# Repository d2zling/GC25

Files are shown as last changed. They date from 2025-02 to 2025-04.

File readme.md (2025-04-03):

<div STYLE="page-break-after: always;"><div>

# 智能物流电控技术总结

* [ ] 作者：祝晓立（D2zling）

本次物流从前期验证到最终实现所有功能花了很多时间，吸取了之前的经验，也有新技术的应用，本文章把我所完成的智能物流的电控方向所用技术总结起来，方便以后随时阅读和查看。

运行视频：[物流小车_哔哩哔哩_bilibili](https://www.bilibili.com/video/BV1aeZmYMEMx/?spm_id_from=333.1007.0.0)

---

### 着重关注问题

* **堆叠式PCB**设计
* 整机**线路走线规划**
* **易于调试**的代码架构
* **底盘**运动控制技术
* **机械臂**运动控制算法

围绕以上问题，结合结构和视觉的需求，电控开始进行从硬件电路到软件驱动、算法层面的全面设计。

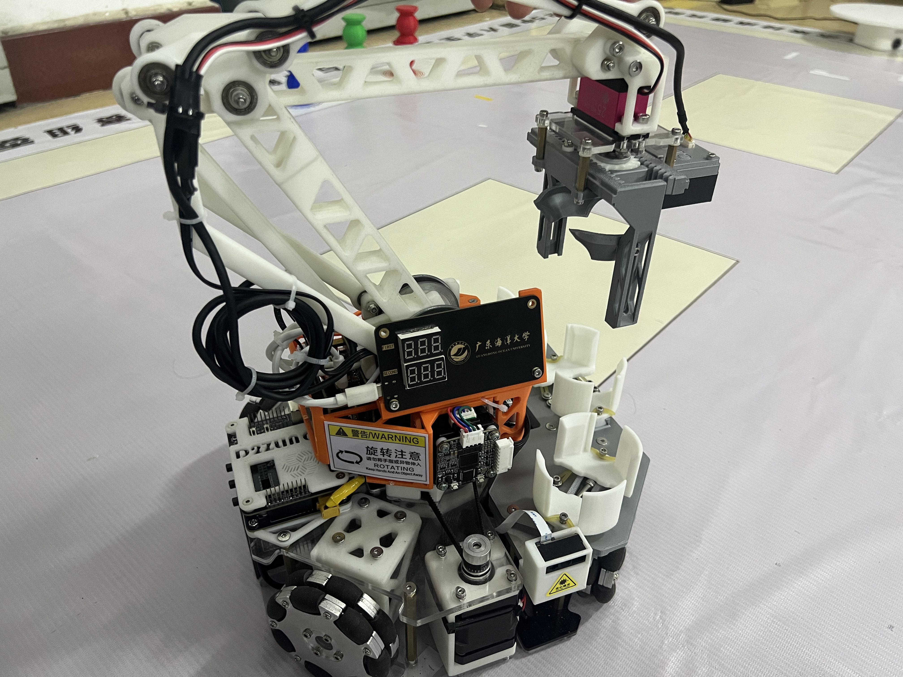
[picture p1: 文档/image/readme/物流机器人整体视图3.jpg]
整体视图


---

### 硬件设计

#### 概览

本次PCB最重要的设计思路就是堆叠式PCB设计，堆叠式PCB可以实现更快的**电路维修**，替换，实现电路的**模块化**，充分利用**垂直空间**。例如功率板和主控板的堆叠设计，充分利用了物流车的垂直空间，调试时主控板损坏，又或者主控板需要替换升级，我们只需要替换掉主控板就可以了，不需要维护功率板。截止到校赛，一共设计了四块PCB，分别是**功率板**、**主控板**、**云台顶部、底部分线板、**显示板、灯光板、泰山派拓展版等。功率板连接电池，负责整车电源控制，主控板使用**STM32F4**主控，引出多种通讯接口，满足各种外设控制需求。分线板通过40pin的FC排线连接主控板，然后引出各种接口，接电机、树莓派（泰山派）等设备。显示板使用74hc595串行芯片实现控制数码管显示任务码。具体文件可以参考[PCB\25工创PCB.eprj](./PCB/25工创PCB.eprj)文件，PCB文件使用嘉立创绘制。

<div STYLE="page-break-after: always;"><div>

* 下图展示各块PCB的连接方式

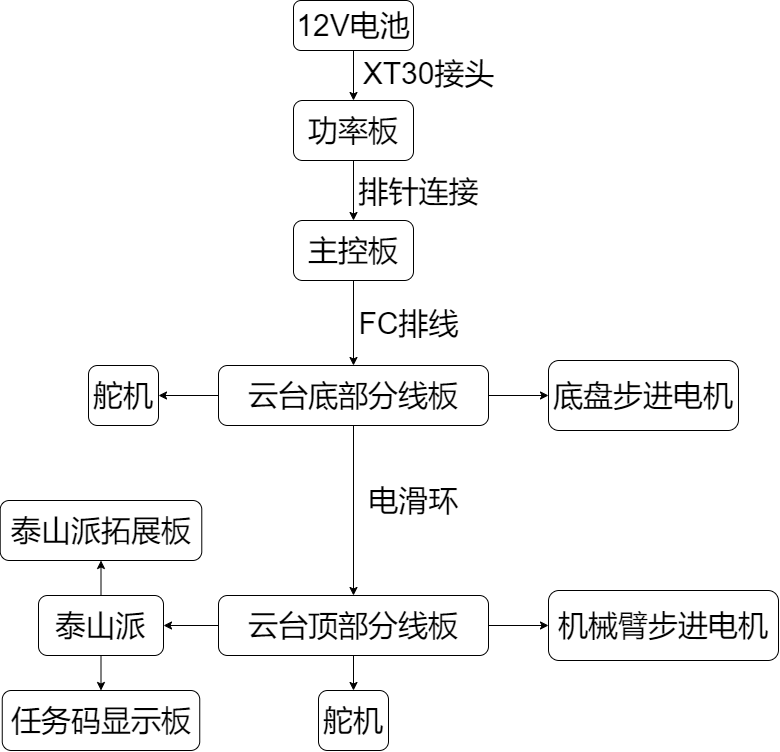
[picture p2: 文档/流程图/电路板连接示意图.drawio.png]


#### 功率板

功率板具有升压和降压功能为整个物流车提供电源，搭载两路升压电源和两路降压电源，升压使用传统**boost**拓扑电路从电源电压**12v升压到24v**，供电机或者其他需要高功率用电器使用，使用**XL6019**，有最大5A的开关电流，因为电机功率比较大，这里选择两路同样的升压芯片，每路XL6019驱动四个步进电机，总共驱动八个。降压使用**buck**拓扑电路，分为两种降压电压，分别是降压到6v和5v，降压到**6v**给舵机使用，降压到**5v**给芯片、树莓派（泰山派）等使用，使用的是**TPS5430ADDR**，可以输出3A的连续电流，还是**宽输入**的可以输入5.5V到36V，对于驱动一些芯片或者舵机来说绰绰有余。更加具体的芯片信息可以从他的**数据手册**上找到，包括输出电压调整，典型应用等，这里不再赘述。

在设计功率板时，除了**电路完整性**之外，还要注意每个部分使用起来是否**便利**，比如功率板在设计时，我将三路（24v、6v、5v）电源输出都做了**单独开关**，调试物流车时可以单独开关三路电源，更加方便调车。另外要从升降压芯片**输入端**做开关控制，防止功率板关断不完全，如果从芯片输出端做开关控制，虽然电源开关是关断了，但是实际芯片还在从输入端供电，持续损耗电源的电，也就是没有完全断电。功率板输入接口选择**XT30**，这个接头是航模接头，很稳固，大小合适而且也好看。电源输入端还连着一个DC接头，有了这个DC接头，不但可以多一个电源输入接头，能兼容更多电池接口，平时还可以实现不断开电池的XT30接头，直接用这个DC头充电，更加的便利。大家设计PCB时可以参考功率板的设计，都是经过测试的方案，基本不会出现问题。另外在设计电路接口的时候，还可以多多上**淘宝**看看各种连接器，比如一些加高排母等连接器，可以让你的PCB调车的时候使用起来更加便携。

* 功率板原理图

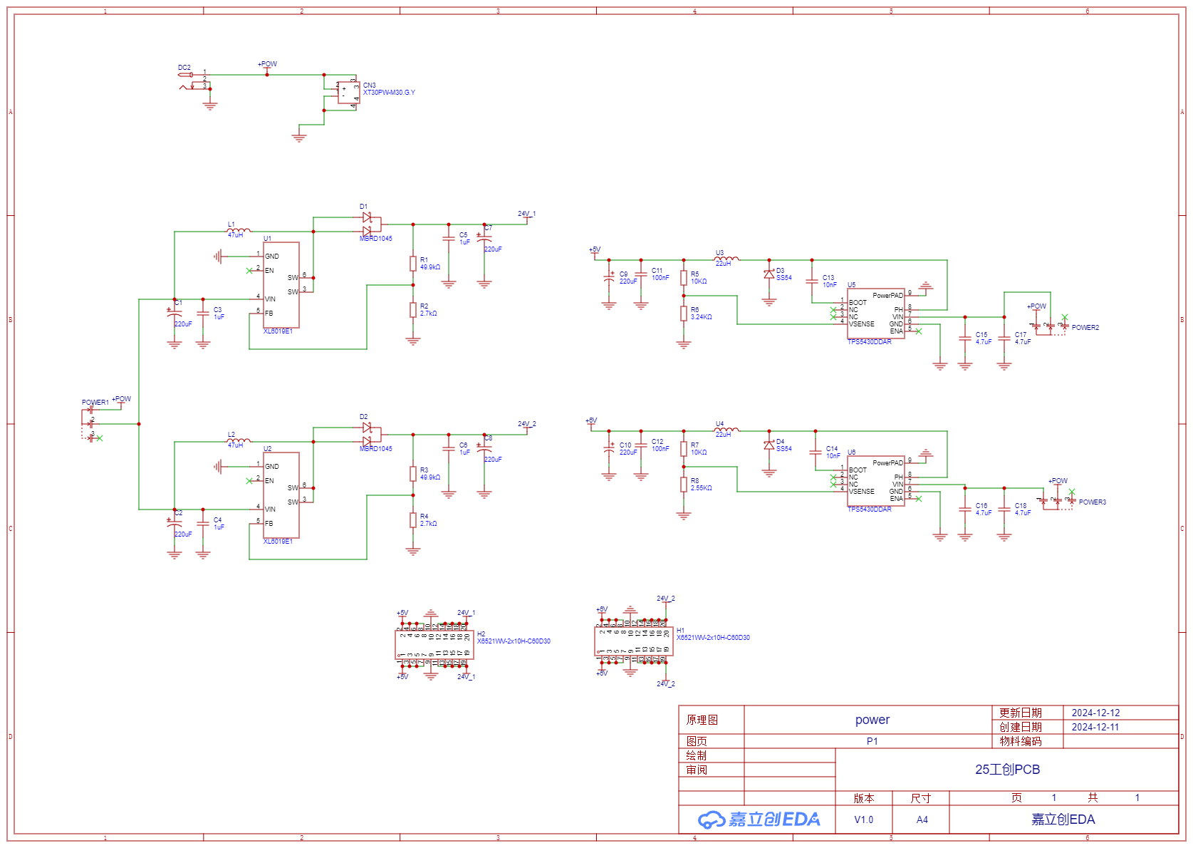
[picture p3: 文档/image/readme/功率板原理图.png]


功率板的**布局布线**要特别注意，因为是控制电源的，如果电源不稳，会出现很多莫名其妙的问题，重打一块PCB的时间成本一般在6~10天时间成本是很高的，所以我们设计PCB要争取一版做好。功率走线一定要粗，这里的功率走线使用了铺铜+开窗的方法增大过流能力，开窗之后可以在铜箔上铺一层锡，增大过流面积，下图使用黄色线勾勒的铜箔就是使用铺铜+开窗增大过流能力的例子。电源除了铜箔走线要粗，反馈线也要布局好，**反馈线很大程度上决定了电源稳不稳定**，下图标了数字1234的四条导线都是反馈线，无论是buck还是boost电路，都有**反馈（FB）引脚**要从输出电容附近取电，因为经过输出电容的电压是最稳的，最适合来做电压反馈的。设计电源的时候要分清哪些是**功率走线**，哪些是**信号走线**，功率走线尽量短和直，还有一定要够粗，信号线要走干扰少的地方，高频回路面积要小。另外，在可能发热的地方还可以多打散热孔，像是功率板的XL6019底下和TPS5430ADDR底下都有几个过孔增加散热。

* 功率板底层layout

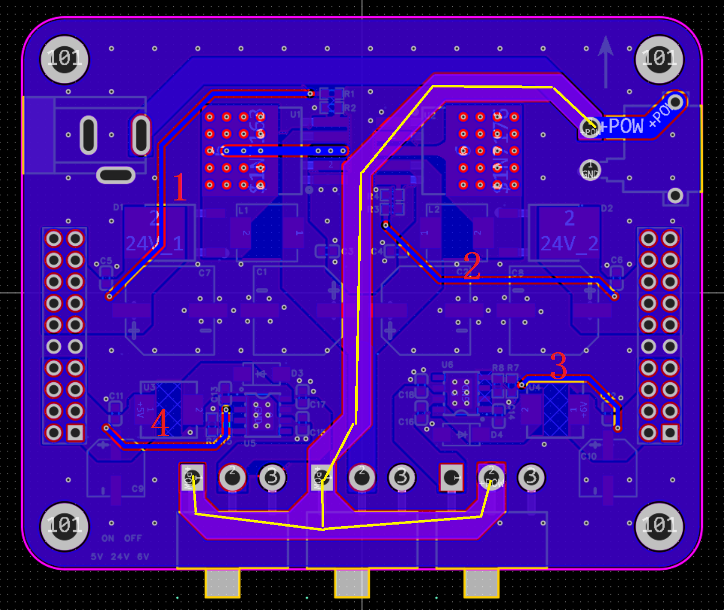
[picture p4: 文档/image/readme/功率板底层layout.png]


由于功率板涉及到**堆叠pcb**设计 ，在设计的时候我们并不确定某些元器件会不会和另外一块电路板有**干涉**，所以我们可以充分利用嘉立创的导出3D模型的功能，导出step文件，利用**solidworks**将两块电路板组合成一个装配体，可以大概的查看元器件有没有干涉，如下图所示。

* 3d模型图

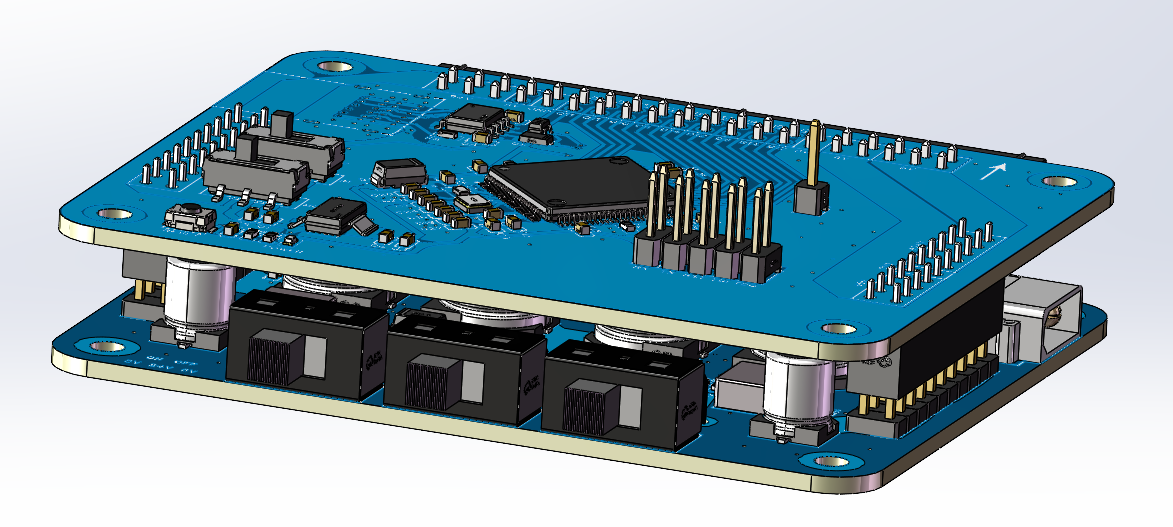
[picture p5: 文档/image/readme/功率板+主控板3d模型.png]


#### 主控板

主控板是整个物流车的核心，主控使用的是**STM32F407VET6**，选择这颗芯片的原因是第一个熟悉，第二个价格合适，外设刚好够用，性能绰绰有余，主控板集成了一个**CH340N**串口转USB芯片和一个**AMS1117**降压芯片，给芯片提供3.3V工作电压。还有两个**单独**开关，分别控制双层typec接口的电源和芯片的电源，设计上可以单独打开芯片或者typec电源，更加便于调试。还留了一个**无线DAP烧录器**的调试接口，支持远程串口，可以远程下载程序。主控板的布局布线比较简单，只要能连通基本就能工作，但是要注意，芯片的**去耦电容**要摆放在芯片的供电引脚旁边，保证电源的质量，去耦电容的**大小和数量**在芯片手册可以找到。主控板通过一个40pin的FC排线输出信号和电源，有12路24V电源，4路6V，两路5V，剩下的都是信号线，大部分时串口线，还预留了4根引脚，可以扩展功能。

* 主控板顶层layout

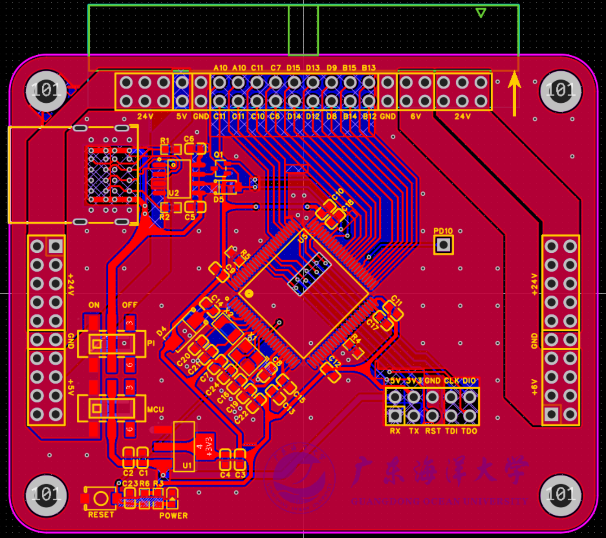
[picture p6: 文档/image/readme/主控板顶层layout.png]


主控芯片的原理图可以直接使用，STM32F407的**PD10**引脚单独引出的原因是为了**测量程序运行的时间**，在程序需要计时的地方加一行反转PD10引脚的电平然后配合示波器就可以测量出程序运行的时间，可以看整个系统的时间响应情况。主控板原理图里比较有意思的是CH340N的**防倒灌电路**由一个二极管和一个三极管组成，在CH340手册里面有描述它们的作用，这里的主要目的是为了防止视觉模块通过CH340N的**TX和RX引脚**反向供电给STM32导致STM32无法关机，之前就遇到过**关闭不完全**的情况，导致芯片看上去断电实则还在运行，调试的时候就没那么方便。板载还有一颗LDO用的是常用的AMS1117，是用于5V降压到3.3V。目前只有一个指示3.3V的LED，主控板之后还可以改进给每一路电源做一个LED显示是否开启，不然在调试的时候经常分不清哪些开关时打开的，哪些时关闭的。

<div STYLE="page-break-after: always;"><div>

* 主控板原理图

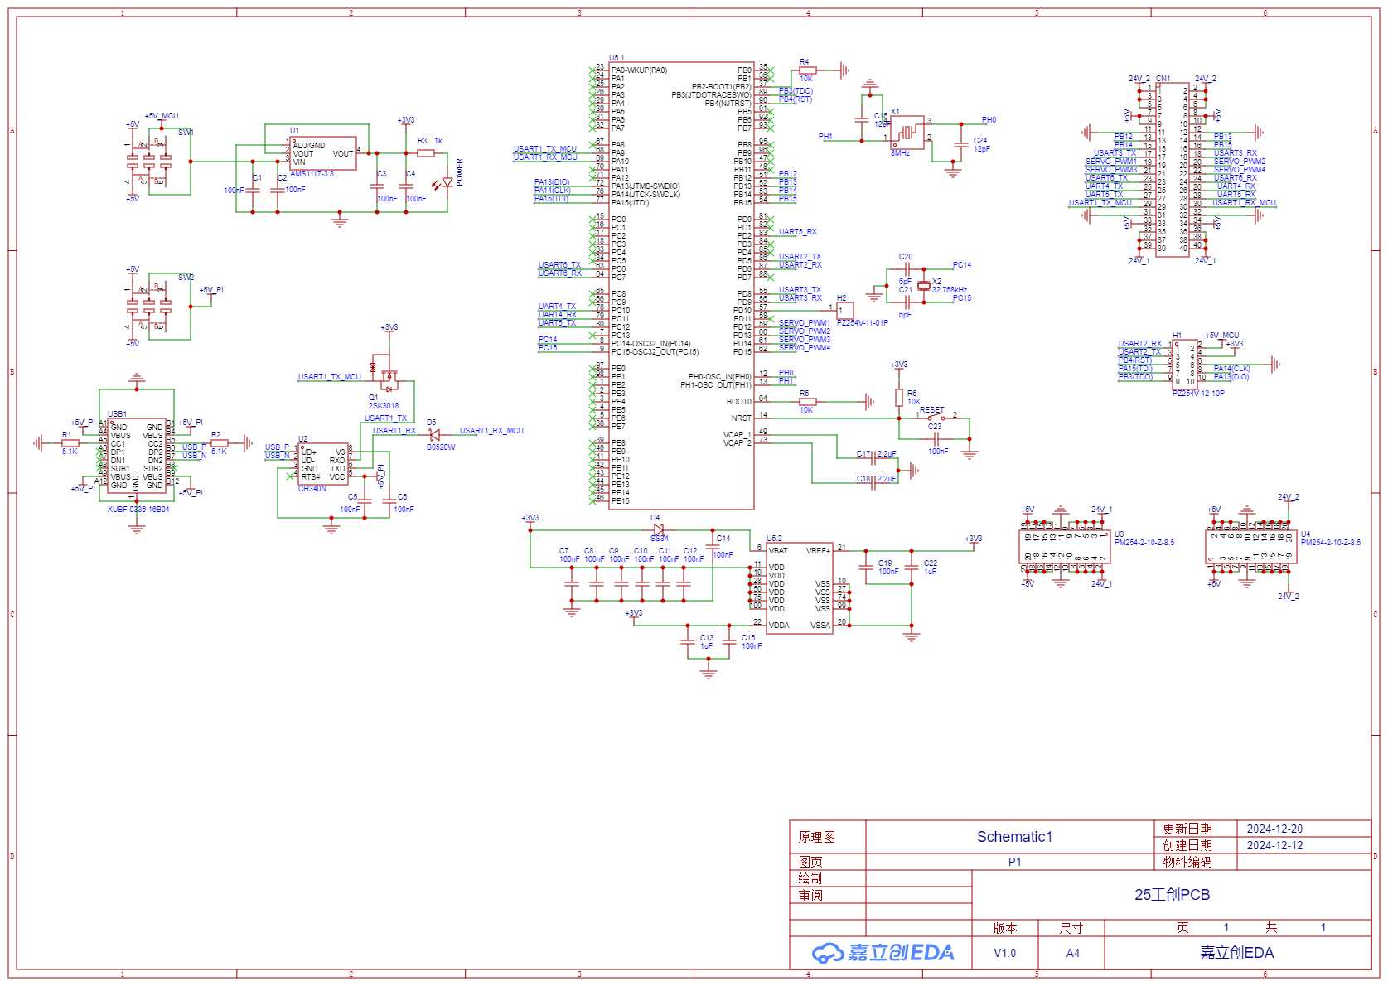
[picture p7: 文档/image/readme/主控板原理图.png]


* 功率板+主控板堆叠设计实物图

<div style="text-align: center;">堆叠设计</div>

可以注意到的是，功率板和主控板设计了很多**开关**，加起来一共有五个， 下面三个是控制24V、6V、5V的上面两个是在5V的基础上再加两个开关，控制5V上的主控芯片和外接视觉模块的供电，这样的好处是我们可以**单独调试**某些功能，而让其他功能不工作。举个例子，如调试舵机的时候，我不希望电机上电，那么我们只要接通6V和5V和主控芯片的电源就可以调试了，电机是完全断电的状态，可以加快工作效率。

#### 分线板

设计分线板的目的是为了**更简洁**的接线，还有把**陀螺仪**放在物流车的**机械中心**。分线板分为**两块**，一块是在云台下面，另外一个是云台上面，通过电滑环连接。分线板大部分是接口元件，还有一个AMS1117从5V降到3.3V供陀螺仪使用。由于分线板是放在机器内部，比较难拆出来，所以设计的时候就想着要电路要简洁可靠，基本没有什么元件，这样才可靠性高，可靠性高意味着不用经常拆出来维护，最终设计出来的效果也确实如此，上面只有两个元器件，一个是降压芯片还有一个陀螺仪，其他都是接口，连接电机、舵机等各种设备。平时容易出问题的PCB都放在机器外面比较好拆卸的地方，通过一个40pin的FC排线连接分线板，拆卸的时候只要拆出排线和几颗螺丝就能拆除主控板和功率板，这种设计更能提高维护效率。在设计分线板的原理图的时候要注意**FC排线线序**的问题，不然线序错了接上就烧了。

* 云台底部分线板原理图

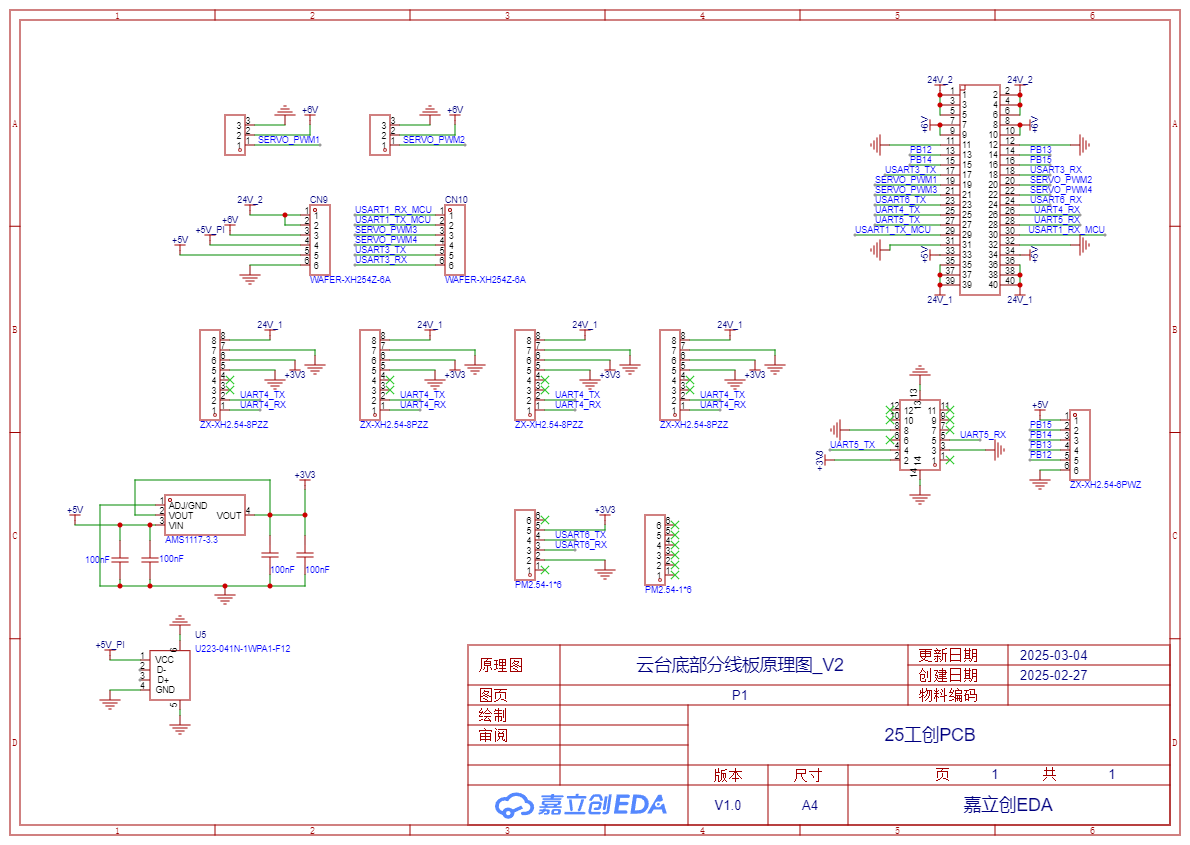
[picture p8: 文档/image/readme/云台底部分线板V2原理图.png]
分线板


PCB的外形可以让结构同学规划，然后把DXF文件导出，利用嘉立创的DXF文件导入功能就可以导入外形文件，这样就不用担心外形会冲突，分线板的外形就是结构同学规划的。关于分线板的layout基本不用注意什么东西，只要功率走线够粗就行，最主要的是设计的要便利，分线板出线位置要和电机等设备的位置一一对应。关于连接件的选取可以多逛逛淘宝，很多方案都是在淘宝看到才了解到的，比如是主控板的双层typec接口。

* 云台底部分线板顶层layout

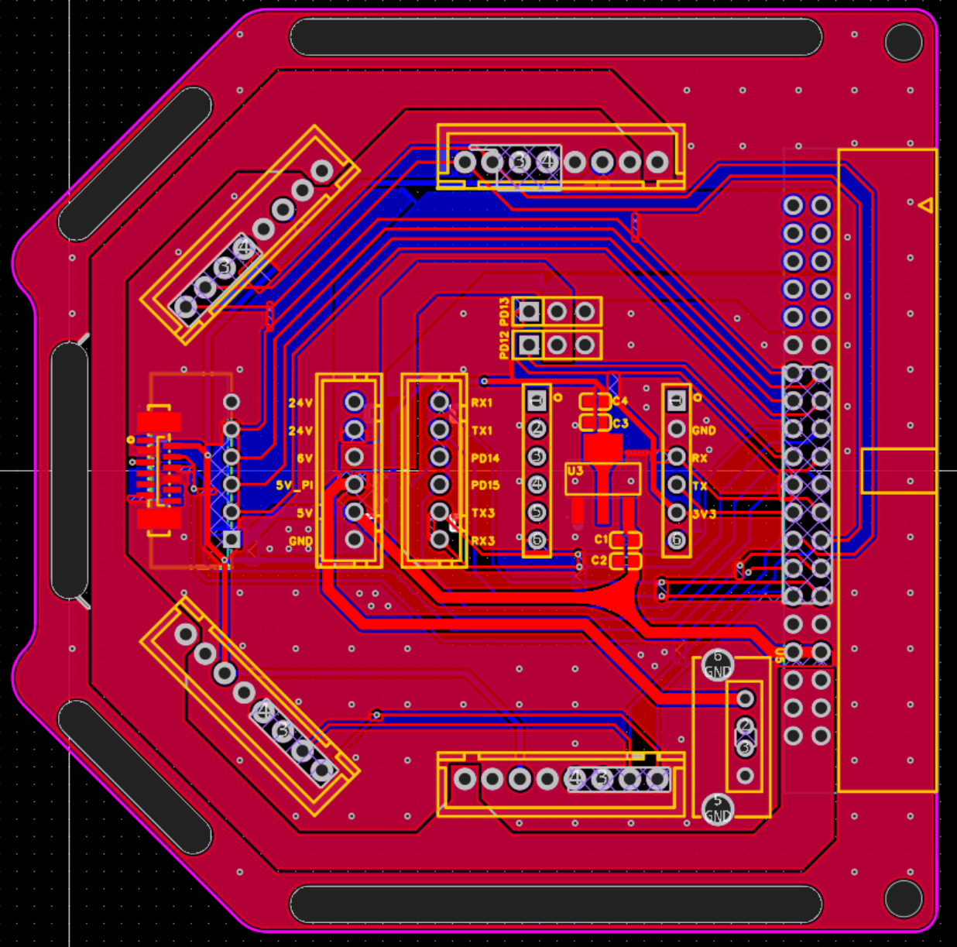
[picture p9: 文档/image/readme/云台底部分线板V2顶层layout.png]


* 云台顶部分线板原理图
  云台顶部分线板预留了泰山派供电，泰山派通讯，云台电机通讯，舵机控制。

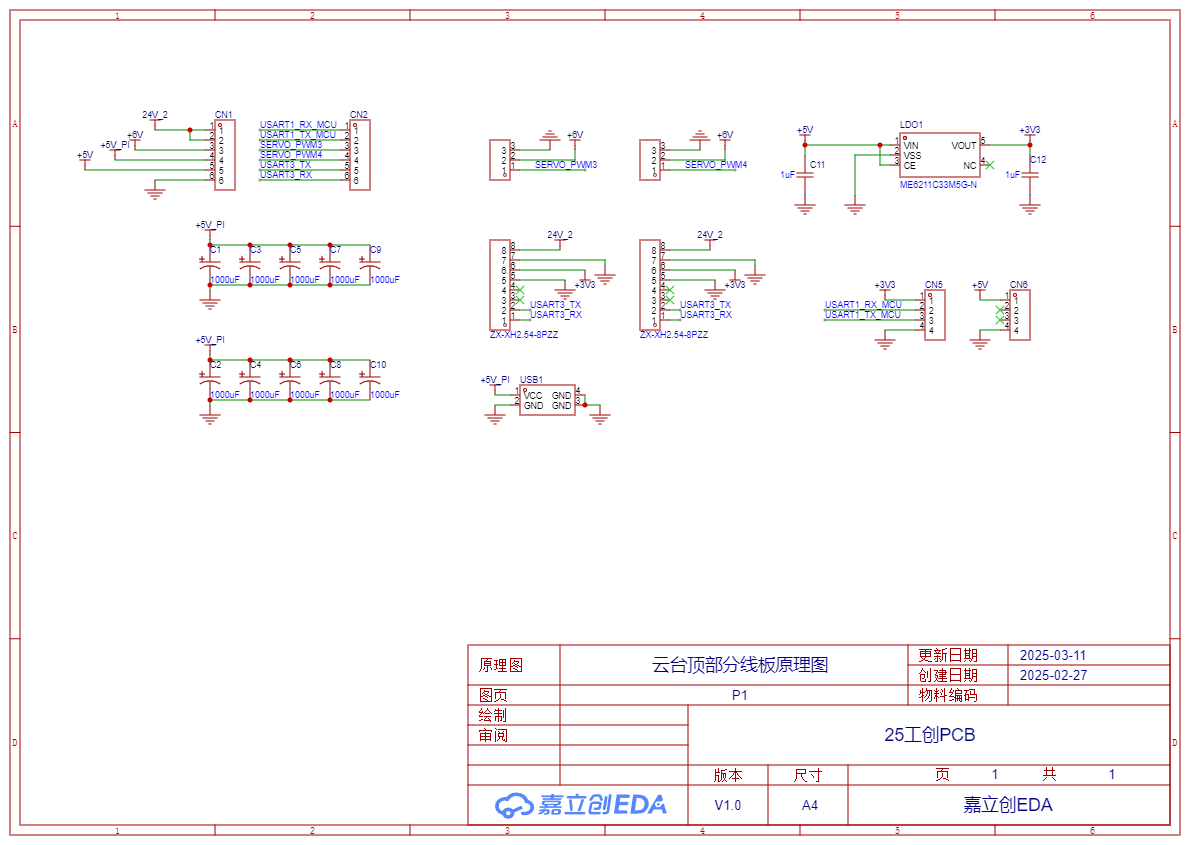
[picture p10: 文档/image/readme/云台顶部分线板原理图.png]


* 云台顶部分线板layout

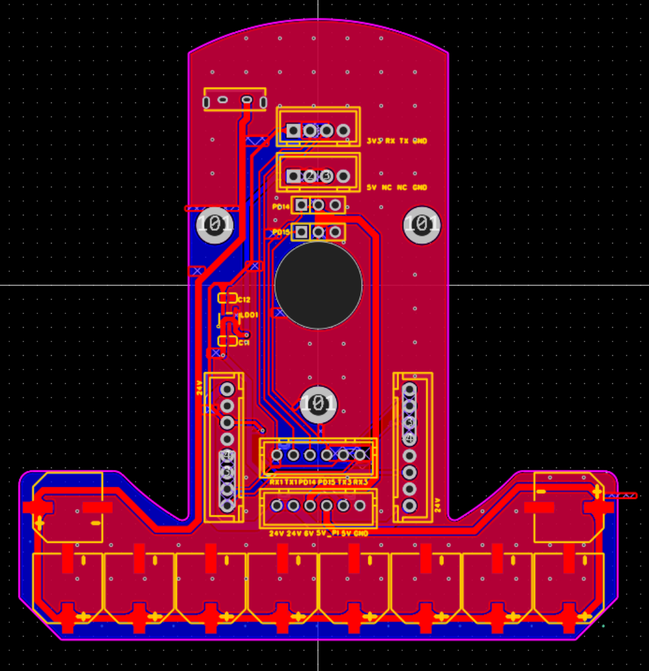
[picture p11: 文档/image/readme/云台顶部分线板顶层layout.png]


顶部分线板在给视觉模块（泰山派）那路装了很多电容，全部加起来有1F，设计的目的是放置泰山派在电机启动时造成整车低电压导致泰山派重启。

#### 显示板

* 显示板原理图

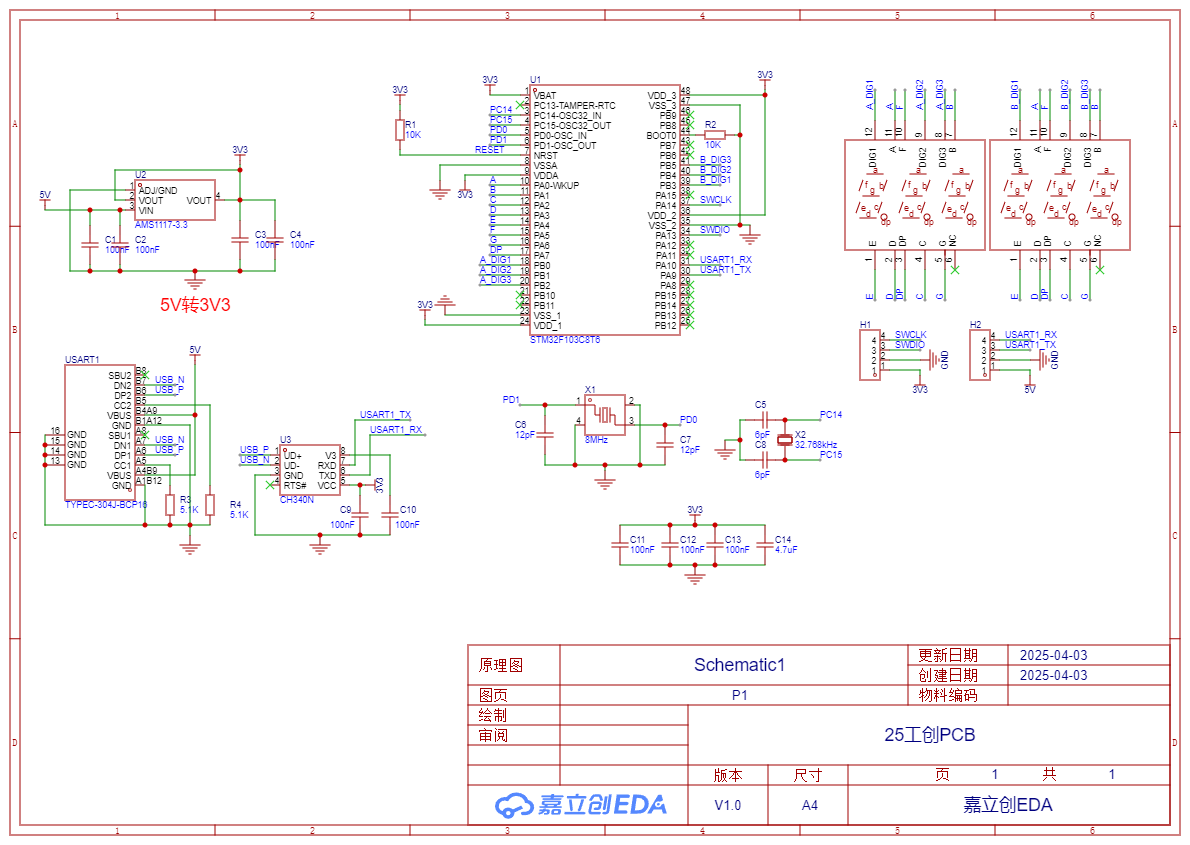
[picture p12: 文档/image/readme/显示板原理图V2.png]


* 显示板顶层layout

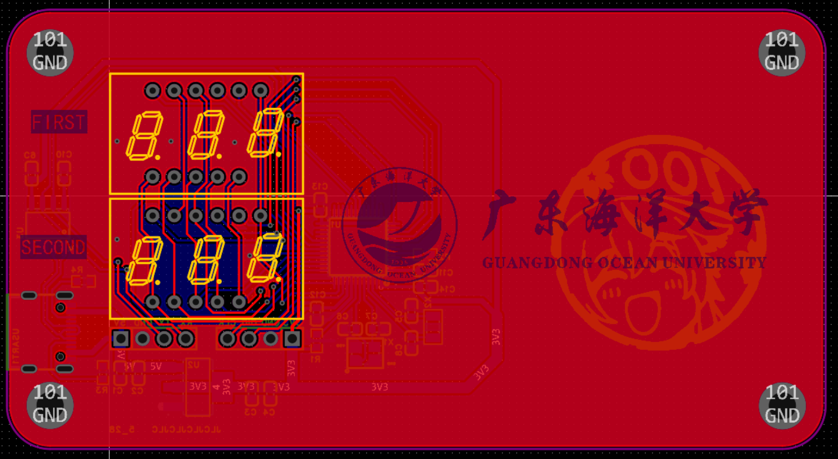
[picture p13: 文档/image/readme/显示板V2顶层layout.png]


#### 灯光板

灯光板设计目的是为了给视觉补光，做了个环形光源。使用stc15w204s单片机，仅有8根引脚，十分适合来控制rgb灯珠。灯珠用的是ws2812。

* 灯光板原理图

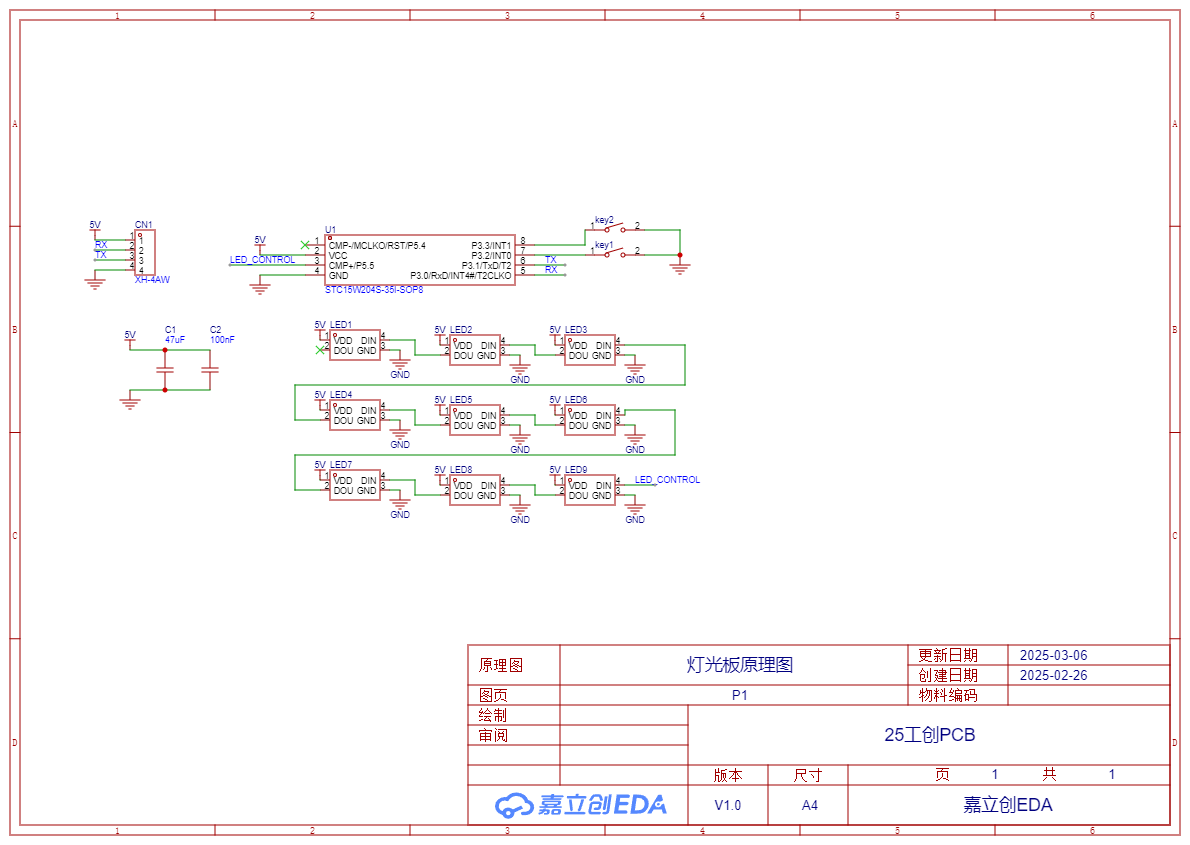
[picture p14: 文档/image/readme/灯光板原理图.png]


如下图所示环形光源

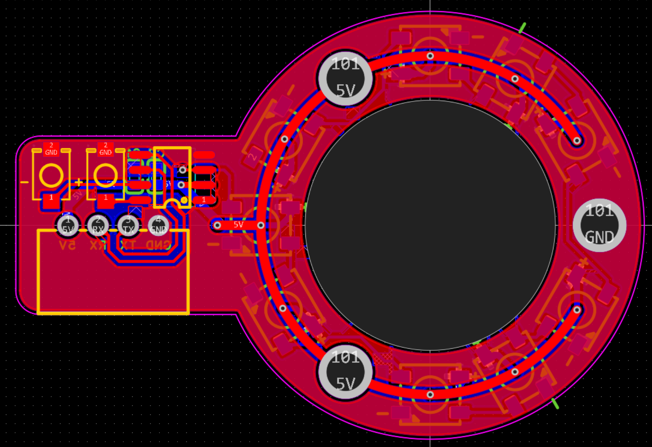
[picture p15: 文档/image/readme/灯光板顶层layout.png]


#### 泰山派再拓展版

此PCB见视觉部分文档。

#### * **注意**

1. 在功率板上并没有集成3.3V电压的降压芯片，因为3.3V电压太低，容易受干扰，最好在需要3.3V的场合单独接一个**AMS1117**或者其他替代LDO芯片，来给STM32F407和其他需要3.3V的使用。舵机单独6V原因是因为舵机的电流大，与其他用电器共一路会引起电压波动，严重的会造成树莓派等重启。
2. ~~目前电路板还存在电机上电时**电压不稳**的情况，推测是电池的电流输出能力不够或者升降压芯片的动态响应不够好的原因，会在电机上电时造成其他路有个瞬间低电压，造成其他路设备重启，可以尝试**增大输出电容**来解决这个问题。~~（已解决，解决方案在顶部分线板与泰山派连接的5v电源升压到6v，另外添加1F电容作为低谷储能电容，实测5000uf电容就可以）
3. ~~主控板的双层typec接口目前会概率出现无法识别的情况，估计是识别电阻的问题，可以通过换用更熟悉的单层typec接口来解决或者是尝试更换识别电阻。~~（已解决，解决方案直接使用stm32f4串口连接视觉设备串口，不通过USB）
4. ~~为了显示板的布线考虑，原理图74HC595连接数码管的方式是乱序的，编写驱动程序的时候要注意。~~（74HC595芯片的显示板不使用，原因：电路板功能验证未通过，改用V2任务码显示板）

---

<div STYLE="page-break-after: always;"><div>

### 运动算法设计

#### 概览

工程使用的算法大概可以分为三种，分别是底**盘控制**算法，**机械臂控制**算法，5阶**插值**算法。

#### 底盘控制算法

关于底盘的控制算法，不同的驱动方式有不同的算法，经过考虑，整车选择了全向轮作为驱动机构，四个全向轮组成**O**形，实现全向移动。算法原理很简单，只需要用到速度矢量的分解，三个速度矢量分别是方向x速度、y方向速度和角速度w，其中x和y垂直且与组成的平面平行于地面，分解为四个全向轮的速度。

具体推导可以参考以下文章：`https://blog.csdn.net/weixin_42722140/article/details/134621461`

需要注意的是文章通过一个**旋转矩阵**实现了从物流车坐标系到世界坐标系的转换。

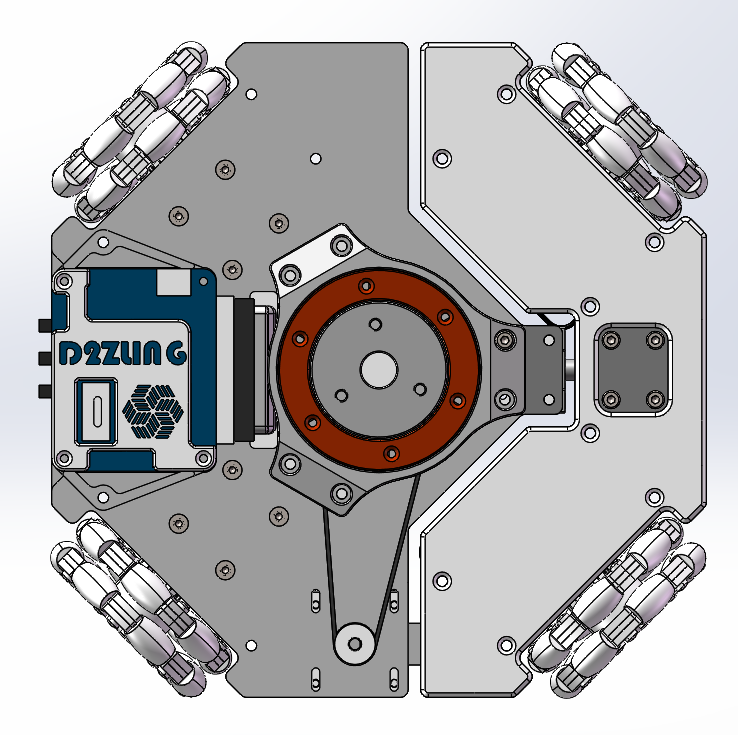
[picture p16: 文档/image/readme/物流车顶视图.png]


#### 机械臂控制算法

机械臂运动学解算分为机械臂运动学正解算和逆解算，正解算是由各个关节的角度推算机械臂末端坐标，逆解算是由机械臂末端坐标推算各个机械臂关节的角度。逆解算用于**控制**，正解算用于机械臂**示教**（校赛暂未实现）。

* 值得注意的是，机械臂算法并没有刻意的去解算计算xy的平面（机械臂底部电机）的角度，仅解算yz平面的角度（大臂角和小臂角度）。xy平面的角度将分离为一个单独调整的变量来控制，这样做的**目的**是更方便的调试动作。

机械臂运动学逆解算算法可以参考以下视频：

```
https://www.bilibili.com/video/BV1mY411476h/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
```

机械臂正解算的思路就像点在平面坐标系移动，已知机械臂的各个臂长和角度，通过三角函数可以推算出每一段的点的x和y所走的距离，叠加各段x和各段的y，最终得到末端坐标。

#### 5阶插值

关于五阶插值的原理可以参考以下文章：`https://www.zhihu.com/tardis/zm/art/269230598?source_id=1005`

简单来说，插值在本工程运动算法的作用是让一段运动变得丝滑，特别是底盘控制，若合理的设置节点的时刻、位移、速度、加速度，5阶线性插值算法能自动解算出一段路径的每个时刻的速度，让物流车运行更加的平稳，**防止车轮打滑**。

前文提到，本次物流车底盘控制算法在底层就是控制x、y、w方向上的速度，在此基础上，分别对这三个方向进行插值，即可实现对一段平滑的轨迹进行控制。下图展示的使用 `matlab`仿真设定x和y方向的每个节点位移、速度、加速度，自动解算出中间过程数值的结果。可以看出，在速度、加速度都是连续的，意味着运动的丝滑。

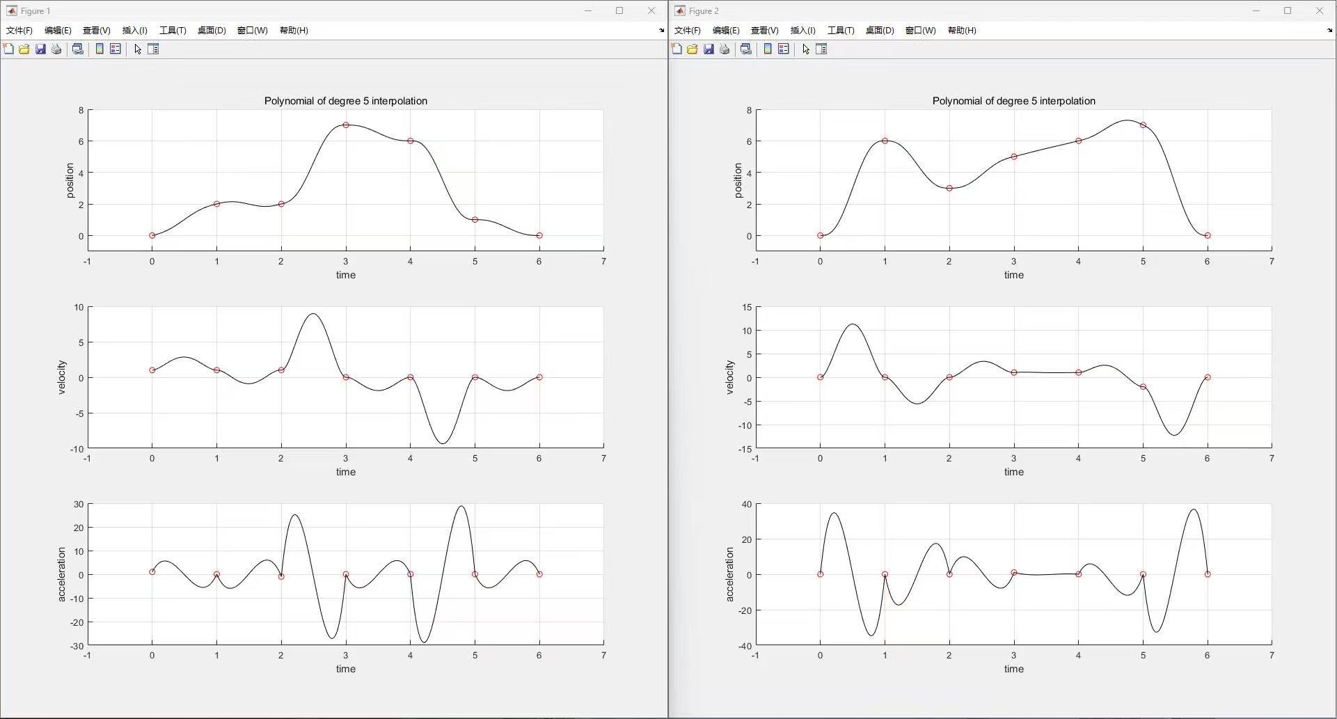
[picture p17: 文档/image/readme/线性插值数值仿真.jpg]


把x和y上的位移作为坐标系的横轴和纵轴，我们可以得出**模拟轨迹**图如下。

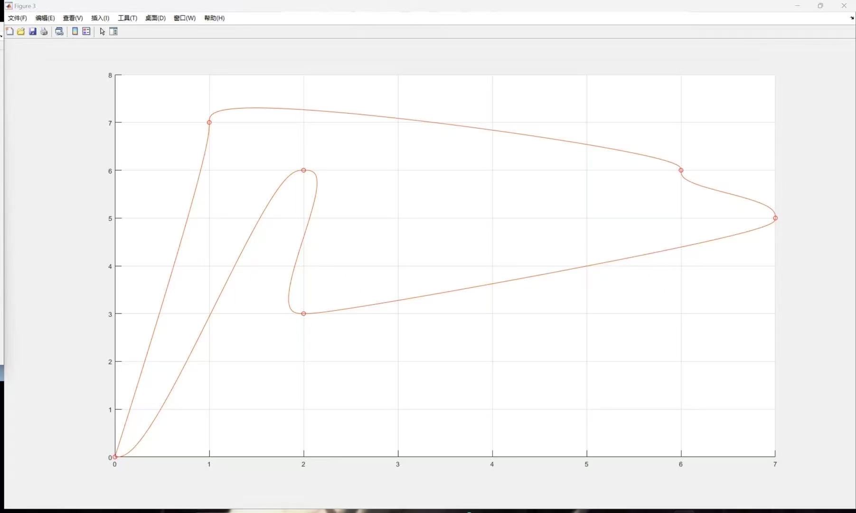
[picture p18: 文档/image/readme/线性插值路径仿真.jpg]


---

### 软件设计

#### 概览

在软件设计上，设计具有层级的代码结构，各层之间**耦合度底**，易于维护升级，可以单独维护升级每一层。在**用户层**，创新性的使用节点的编程思想，将物流车的运动抽象成一个个节点，并通过控制两个节点的状态，自动解算出两个节点间每个时刻的状态，实现稳定快速的物流车控制。调车时，我们只需要修改节点及其节点对应的任务，**其他什么都不需要动**，就可以实现对物流车运动状态进行修改。

#### 文件架构

* 代码文件结构概览（细节的文件暂不展示，后文会详细叙述）

```c
GC_25/
│
└── code/
    ├── .vscode/
    │   └── launch.json		//调试配置文件
    └── remote_control/
    │   └── test.py		//串口通讯测试文件
    │   └── UART.py		//手柄+串口透传遥控
    └── robot_control/
    │   └── CORE		//cotex-m4内核文件
    │   └── FWLIB		//STM32F4外设库
    │	└── DSP			//ARM算法加速库
    │ 	└── SYSTEM		//底层驱动配置
    │	└── HARDWARE 		//硬件驱动层
    │	└── KINEMATICS		//算法层
    │	└── USER		//用户层
    └── digital_tube/		//任务码显示模块工程
    └── led_control/
    	└── led_control		//视觉补光灯工程
```

代码的code-workspace文件在code\robot_control\USER\GC_25.code-workspace，通过这个文件可以打开工程。

**任务码显示模块**使用keil5开发，打开烧录程序即可，通过串口发送类似 `（123312）`指令即可显示，默认波特率115200。

**视觉补光灯模块**使用vscode+EIDE开发，编译后和51单片机一样烧录hex文件就好，使用方法很简单，两个按钮分别是亮度+和亮度-，带掉电存储当前亮度。

主要讲解robot_control工程。

工程共使用了两个库，一个是**stm32标准库**，另外一个是ARM提供的**DSP**库，可以加速一些数学运算，例如COS、SIN函数。

cotex-m4具备**FPU**，可以加速**单精度浮点数**的运算，本工程开启了FPU，开启的方式很简单，添加以下预处理宏定义即可

```c
__CC_ARM
__TARGET_FPU_VFP
__FPU_PRESENT
```

添加之后可以检查以下**宏定义** `__FPU_USED`是否为1，若为1，则表示启用了FPU，本工程启用了FPU。

工程所有代码都存放在**code**文件夹里面

* **.vscode**是cotex-debug插件自动生成的lauch.json文件，当我们需要调试时，需要在里面配置调试参数，如目标芯片型号，调试器型号等。
* ~~remote_control~~文件夹存放了早期调试底盘时写的使用PS5手柄操控物流车的驱动程序，现已不使用。具体原理是使用电脑读取手柄数据，然后通过调试器自带的远程串口传输给物流车，实现对物流车的控制，代码使用python编写。
* **robot_control**是本工程核心文件，该文件夹存放了所有STM32代码，其中CORE和FWLIB和DSP不做过多介绍，都是官方库文件。**SYSTEM**文件夹存放了芯片外设驱动文件，包括使用到的定时器、串口和DMA。**HARDWARE**文件夹存放了硬件驱动文件，包括步进电机驱动、陀螺仪驱动、通讯协议驱动、扫码模块驱动、舵机驱动和系统时钟驱动。**KINEMATICS**文件夹存放底盘控制算法、**5阶线性插值算法**和机械臂控制算法文件。最后是**USER**文件夹，存放了平时常用的文件，包括主程序main文件、物流车动作文件、路径控制文件、~~远程遥控文件~~和一些官方的中断服务函数文件等。

在robot_control中，除官方库外，SYSTEM文件是工程**最底层**，描述了片内外设如何初始化，HARDWARE内文件调用SYSTEM层和官方库文件，封装了一层**硬件驱动层**，负责硬件控制。KINEMTICS层负责**整车运动算法**，仅调用HARDWARE层和官方库文件。USER层调用HARDWARE最终实现**运动控制**。

整个工程的**层级结构**为：SYSTEM->HARDWARE->KINEMTICS->USER（SYSTEM为最底层）

另外需要注意的是，部分文件存在**跨层**或者**同层**调用的情况，分别是USER层的 `motion.c`调用了HARDWARE层的 `protocols.h`，和HARDWARE层的 `protocols.h`调用了同层的 `scanner_driver.h`。

#### 开发环境

电控的开发环境是vscode的插件EIDE,具体使用可以参考下面链接：

```
https://www.bilibili.com/video/BV1nr4y1R7Jb/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
```

里面有详细的EIDE配置方法，但是想要使用调试功能，视频里的方法已经不适用，可以参考下面链接：

```
https://blog.csdn.net/qq_39854159/article/details/124511433
```

建议使用vscode的**插件**EIDE和cotex-debug加上openocd。EIDE写代码，编译烧录，cotex-debug负责调试。想要使用调试功能，要注意整个**工程不能有中文路径**，cotex-debug不支持中文路径。配置cotex-debug时需要注意的是**lauch.json**文件，该文件位于code\.vscode\launch.json。需要配置的路径在文件已经标明，目前配置了dap-link和stlink。

jlink也可以使用，支持实时查看变量对于电机或者运动控制等一些需要快速查看变量的场合很方便，使用串口输出调试信息会让整个程序运行效率变慢，对于一些高速任务如需要20KHz控制频率的FOC控制技术，加了一个串口输出函数会极大影响运行效果，这时如果我们还想要监控数据，可以考虑使用jlink。

* 以下为cotex-debug调试的配置文件 `launch.json`的示例（仅需修改注释提示的地方）

```json
"configurations": [
    {
        "cwd": "${workspaceRoot}",
        //需要配置以下elf文件路径
        "executable": "F:\\project_no_cn\\GC_25\\code\\robot_control\\USER\\build\\Template\\GC_25.elf",
	//dap为调试名称，可以更改
        "name": "dap",
        "request": "launch",
        "type": "cortex-debug",
        "servertype": "openocd",
        //需要配置以下openocd文件路径，选择调试设备和目标
        "configFiles": [
            "F:\\vscode_debug\\openocd-0.12.0\\openocd-0.12.0\\tcl\\interface\\cmsis-dap.cfg",
            "F:\\vscode_debug\\openocd-0.12.0\\openocd-0.12.0\\tcl\\target\\stm32f4x.cfg"
        ],
        "searchDir": [],
        "runToEntryPoint": "main",
        "showDevDebugOutput": "none"
    },
```

#### SYSTEM文件

SYSTEM文件主要是负责底层芯片外设驱动。

* delay

`delay.c/.h`文件直接使用的正点原子的delay文件，这里不做过多叙述。

* usart+dma

`usart.c/.h`文件是配置串口1~6，串口2**重定向**到printf()函数。`dma.c/.h`文件是配置串口DMA，包括发送和接收。这两个文件共同组成了硬件通讯最底层。

下表为串口与硬件对应关系（rx_dma表示开启了串口的**dma接收**+串口**空闲中断**）

|  usart1  |  usart2  | usart3 |  uart4  |  uart5  | usart6 |
| :---: | :---: | :---: | :---: | :---: | :----: |
|  rx_dma  |  rx_dma  | NULL | NULL | NULL | rx_dma |
| 视觉模块 | 调试信息 | 机械臂电机 | 底盘电机 | 扫码模块 | 陀螺仪 |

* timer

`timer.c/.h`文件是配置系统定时器文件，主要存放定时器初始化函数。

下表为定时器和功能对应关系

| tim2 | tim4 | tim5 |
| :---: | :---: | :---: |
| 电机PWM控制 | 舵机PWM控制 | 系统时间戳 |

#### HARDWARE文件

HARDWARE文件主要负责硬件驱动和系统时间控制。

* hwt101_driver

`hwt101_driver.c/.h`文件是陀螺仪**HWT101**的驱动，对数据的解包均由中断函数 `USART6_IRQHandler`完成，最后存放于两个全局变量，加速度为 `hwt101_acceleration_data`变量，世界坐标角度为 `abs_degree_data`。另外还有常见的陀螺仪功能，如陀螺仪复位、校准和设置输出速率。

* motor_driver

`motor_driver.c/.h`文件时整车电机驱动，使用以下结构体描述电机：

```c
//电机控制结构体
typedef struct 
{
	char ID;		//电机ID
	char direction;	    	//电机运动方向
	char synchronous;	//同步设定
	int speed;		//速度
	int acc_speed;	    	//加速度
	int pulse_num;	    	//总脉冲数

} steeping_motor;
```

工程创建了7个全局变量**steeping_motor**结构体，用于描述整车7个电机。

```c
extern steeping_motor motor[7];
```

其中 `motor[0]~motor[3]`为**底盘**电机，`motor[4]`为**机械臂小臂**电机，`motor[5]`为**云台底座**电机，`motor[6]`为**机械臂大臂**电机。

另外，除基础的电机速度控制，位置控制外，motor_driver还具有设置电机**零点**，电机回零功能。选择对应的**电机结构体**，设定好结构体参数，**作为参数**传入相应的控制函数即可控制

* protocols

`protocols.c/.h`文件为通讯协议，主要功能处理与视觉模块通讯协议，扫码模块通讯协议~~和远程遥控协议~~。

```c
/**
*@brief 初始化软件数据包
*@param 无
*@return 无
*/
void soft_packet_init(void)
{
	head.next_usart_pack = &tail;
	tail.next_usart_pack = &head;

	pi_location_data.package_header = 'L';
	pi_location_data.package_tail = 'E';
	pi_location_data.packet = pi_location;
	pi_location_data.package_len = 20;
	pi_location_data.package_flag = rec_unfinish;
	create_usart_package(&pi_location_data);
}

```

以上代码创建了一个数据包，该数据包由'L'开头，‘E’结尾，最长20byte个长度。当串口空闲中断触发时，`packet_scan()`内自动索检包头包尾，当包头包尾有创建时，如接收到’L‘开头‘E’结尾数据包，会自动将该数据包的 `pi_location_data.package_flag = rec_finish`用户可以判断该标志位判断是否接收完成，当读取完之后，要手动将该数据包重新置为 `rec_unfinish`，实现以上功能主要使用到**链表**操作。

* scanner_driver

`scanner_driver.c/.h`为扫码模块驱动文件，扫码模块使用串口通讯，由于扫码内容是固定的类似与123+321的数据格式所以我们的驱动也很简单。

* servo_driver

`servo_driver.c/.h`为舵机驱动文件，比较简单，这里也不详细叙述。

* system_clock

`system_clock.c/.h`实现了系统时间戳功能，使用tim5定时中断，系统计时以10ms为步进，每次中断使变量 `sys_time_ms+=10`，然后把 `timer_10ms_flag=1`。若要以10ms运行一个任务，可以参考以下代码：

```c
while(1)
{
    if(timer_10ms_flag)
    {
        timer_10ms_flag = 0;
	task();
    }
}
```

`sys_time_ms`与 `timer_10ms_flag`均为全局变量，`sys_time_ms`是系统运行时间戳。

另外，该文件还实现了计时功能，计时器抽象为如下结构体：

```c
typedef struct _sys_count_time_t 
{
    char count_time_state;
    long long int start_time;
    long long int count_now_time;
    long long int count_end_time;

}sys_count_time_t;
```

若要使用计时功能，需要创建结构体，创建结构体时只需要设定 `count_end_time`的值，开始计时要调用库函数内的 `start_count_time`函数。**注意**，要定期调用 `count_time`函数与系统时间戳同步，调用越频繁计时越准确，最小精确到10ms。

system_clock还集成了时间戳格式化输出功能，可以格式化输出分钟和秒数。

#### KINEMTICS文件

KINEMTICS文件主要负责**运动学算法**的实现。

* chassis_control

`chassis_control.c/.h`负责底盘运动学解算，兼容麦克纳姆轮和全向轮。`set_car_speed_Omni_Wheel`是物流车坐标系下的物流车速度控制，`chassis_control_Omni_Wheel`是世界坐标系下的物流车速度控制，内有角度环控制、世界坐标系转换、全向轮转速转换。

全向轮物流车坐标系下速度解算如下所示

```c
motor[0].speed = - x + y - w;
motor[1].speed = - x + y + w;
motor[2].speed = x + y - w;
motor[3].speed = x + y + w;
```

麦轮不赘述。

* robot_arm_control

`robot_arm_control.c/.h`负责机械臂运动学解算，包含机械臂运动学正解算 `robot_arm_calculate_forward`，逆解算 `robot_arm_calculate_inverse`，机械臂底座控制robot_arm_control_botton_position，机械臂臂控制 `robot_arm_control_arm_poosition`。

另外宏定义还定义了以下机械臂规格，使用的时候可以修改

```
//机械臂关节减速比
#define reduction_ratio     4.0f

//机械臂规格，单位为mm
#define base_height         92.3f  //底座高度
#define first_arm_lenght    180.0f //第一个关节长度
#define second_arm_lenght   180.0f //第二个关节长度
#define gripper_lenght      0.0f   //机械爪长度
#define gripper_height      0.0f   //机械爪高度
```

* linear_interpolation

`linear_interpolation.c/.h`负责5阶插值算法的实现，文件以节点的形式描述。每个阶段有对应的输入参数、5阶方程解、节点队列分别用以下结构体表示：

```c
typedef struct _input_li5_t
{
    float t0; //开始时间
    float s0; //开始位移
    float v0; //开始速度
    float a0; //开始加速度

    float t1; //结束时间
    float s1; //结束加速度
    float v1; //结束速度
    float a1; //结束加速度

}input_li5_t;

typedef struct _output_li5_t
{
    //解算出五阶方程的7个参数
    float t0;
    float a0;
    float a1;
    float a2;
    float a3;
    float a4;
    float a5;

}output_li5_t;

typedef struct _li5_t
{
    float time;                     //节点时间
    float dis;                      //节点位移
    float vel;                      //节点速度
    float acc;                      //节点加速度

    void * task;                    //节点任务

    output_li5_t solve;             //5阶计算解算结果
}li5_t;w
```

文件中 `li5th_solve`根据推导出的公式求解每一个节点的函数的解，`get_displacement_from_li5`、`get_speed_from_li5`、`get_acceleration_from_li5`分别从已经求解的节点获得该时刻的位移，速度，加速度。

文件中 `solve_li5th_node`自动求解一个5阶插值队列（**li5_t**）的所有函数的解。

#### USER文件

最终调车所需要的文件都存在这里。

* path_control

`path_control.c/.h`是路径控制文件，该文件的存在是为了更快速的编辑物流车任务，达到增大调车效率的效果。`path_control`以队列的形式描述物流车任务。每个队列有单独的路径队列、有单独的路径计时器（获取5阶段插值的结果需要以时间为参数）、有单独的变量指示当前队列运行到什么位置。具体形式以结构体表示，如下所示：

```
typedef struct _path_quene_t
{
    li5_t* quene;           //路径队列
    sys_count_time_t timer; //当前路径节点计时器
    char p_node;            //当前路径节点

}path_quene_t;
```

基于以上结构体，我们可以创建出一个队列对象，控制x方向上的速度，如下所示：

```c
//---------------------------time------dis---speed-----acc--------------//
//创建x轴速度队列
static li5_t node_x_speed[]={{0.0f, 0.0f, 0.0f, 0.0f, NULL},        //出发到扫码区域
                             {1500.0f, 500.0f, 0.5f, 0.0f, NULL},
                             {3000.0f, 740.0f, 0.0f, 0.0f, NULL},
                             {.task =  qr_code_task},               //扫码区域到转盘区域
                             {3000.0f, 1000.0f, 0.0f, 0.0f, NULL},
                             {.task =  rotator_task},               //转盘区域到粗加工区域
                             {1500.0f, -550.0f, 0.0f, 0.0f, NULL},
                             {6000.0f, -450.0f, 0.0f, 0.0f, NULL},
                             {.task =  processing_area_task},       //粗加工区域到精加工区域
                             {2500.0f, 950.0f, 0.1f, 0.0f, NULL},
                             {4000.0f, 1000.0f, 0.0f, 0.0f, NULL},
                             {.task =  processing_area_task},       //精加工区到转盘
                             {2000.0f, -100.0f, -0.2f, 0.0f, NULL},
                             {4000.0f, -600.0f, 0.0f, 0.0f, NULL},
                             //二程
                             {.task =  rotator_task},               //转盘区域到粗加工区
                             {1500.0f, -550.0f, 0.0f, 0.0f, NULL},
                             {6000.0f, -450.0f, 0.0f, 0.0f, NULL},
                             {.task =  processing_area_task},       //粗加工区域到精加工区域
                             {2500.0f, 950.0f, 0.1f, 0.0f, NULL},
                             {4000.0f, 1000.0f, 0.0f, 0.0f, NULL},
                             //回家
                             {.task =  processing_area_task},
                             {6000.0f, -2000.0f, 0.0f, 0.0f, NULL},
                             {9000.0f, -2100.0f, 0.0f, 0.0f, NULL},
                             {.task =  &end_quene}};

static path_quene_t x_speed = {.quene = node_x_speed, .timer.count_end_time = 0xFFFFFFFF};
```

可以看到，以上创建了一个名为x_speed的结构体，包含了一个计时时间被设置为0XFFFFFFFF的定时器，还有一个node_x_speed的队列。需要注意的是，创建队列时，不能连续两次创建节点任务。

文件中 `chassis_path_control`是推演函数，推演每个时刻5阶插值的速度输出，函数具体内容较为复杂，感兴趣的可以看一下，函数具体用法如下所示（此段代码在main.c：

```c
    while(1)
    {
        if(timer_10ms_flag)
        {
            timer_10ms_flag = 0;

            _x_speed = chassis_path_control(&x_speed, out_type_speed);
            _y_speed = chassis_path_control(&y_speed, out_type_speed);
            _w_dis = chassis_path_control(&w_dis, out_type_displacement);

            chassis_control_Omni_Wheel(_x_speed, _y_speed, _w_dis);
            robot_arm_control_botton_speed_CL(_abs_robot_arm_angle);
        }  
}
```

`robot_arm_control_botton_speed_CL`函数是在底盘运行轨迹时使机械臂保持在 `_abs_robot_arm_angle`角度，该角度为世界坐标系的角度。

* motion

`motion.c/.h`文件是除底盘外动作文件，是车动作的具体实现，其中 `motion.h`定义了许多位置坐标，修改时主要修改此位置坐标。

* main

`main.c/.h`文件有着程序的**入口**，程序开始先进行各种设备的初始化，接着创建三个方向的插值速度队列，接着求解三个方向每个节点的解，最后每**10ms推演一次**路径。每推演一次路径解算一次该时刻三个方向的队列的速度，若推演到该节点有任务，则优先完成该节点的任务。整个程序以底盘运动三轴速度为主线，其中添加各种任务节点。

在使用的时候，比如需要调整x速度队列某个节点的速度，我们只需要往node_x_speed结构体数组**添加、修改、删除节点**即可。添加任务时，节点可单独使用.task成员指向对应函数，即可在这个节点添加一个自定义任务。

* ~~remote_car_control~~

已弃用，不做介绍。

---

### TODO

无

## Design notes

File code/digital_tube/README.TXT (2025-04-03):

这个文件是数码管模块的源代码，上面使用一颗stm32单片机控制，
连接串口即可使用，协议为(xxxxxx)，其中两个括号是数据头和数据
尾，x为1到3的任意数字

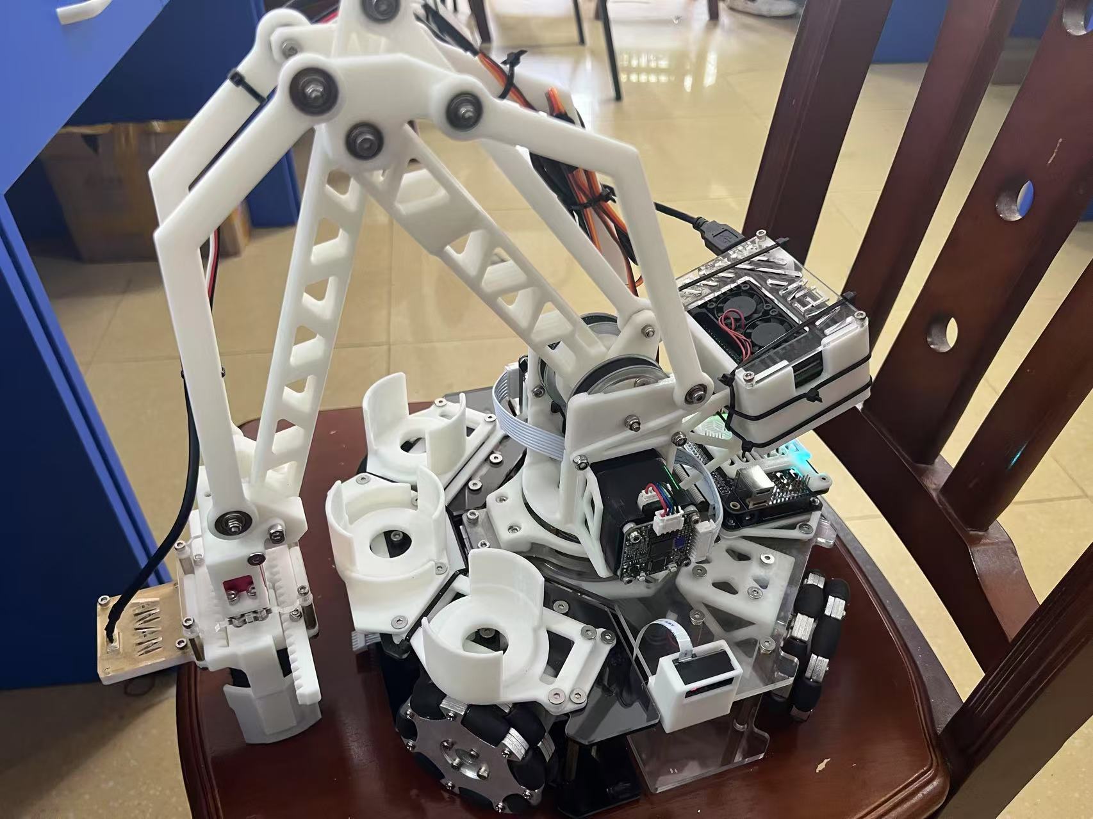
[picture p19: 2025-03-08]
文档/image/readme/物流机器人整体视图.jpg

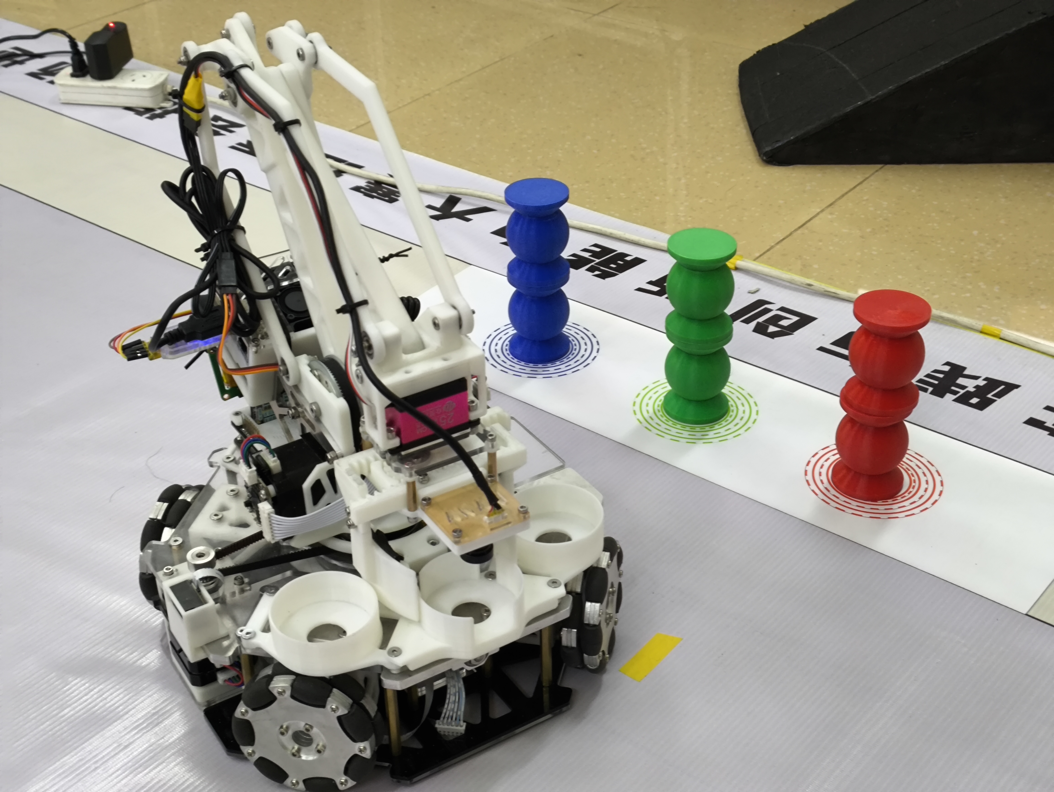
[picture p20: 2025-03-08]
文档/image/readme/物流机器人整体视图2.jpg

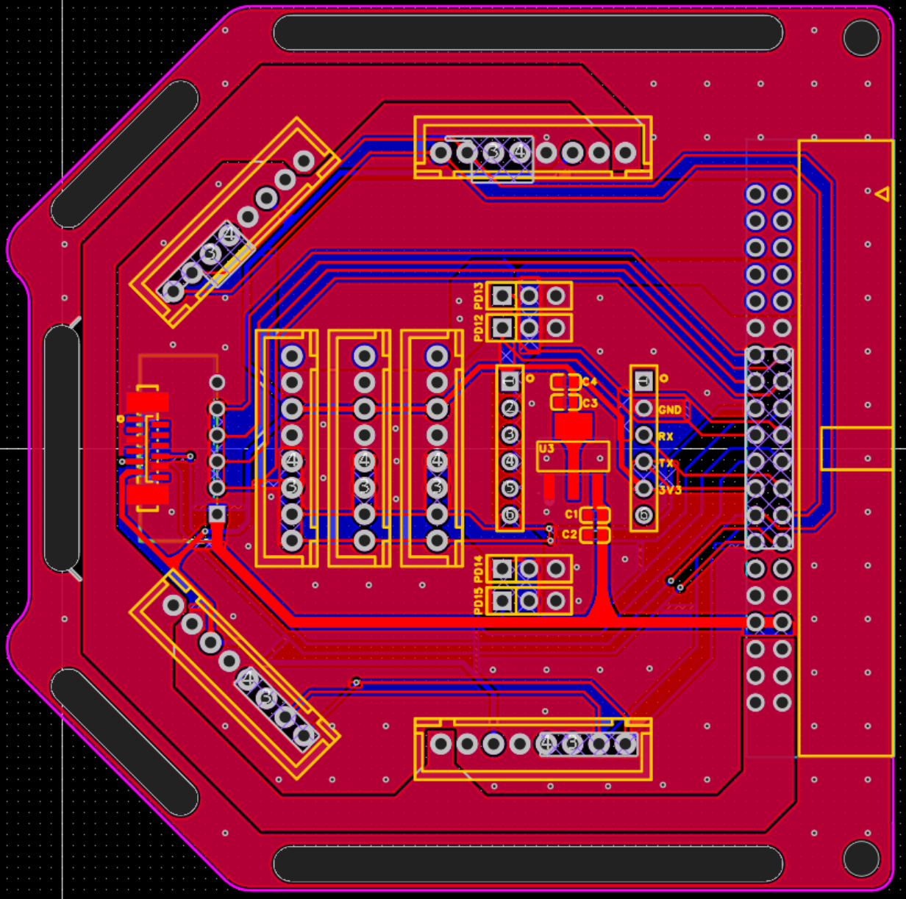
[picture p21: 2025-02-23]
文档/image/readme/分线板顶层layout.png

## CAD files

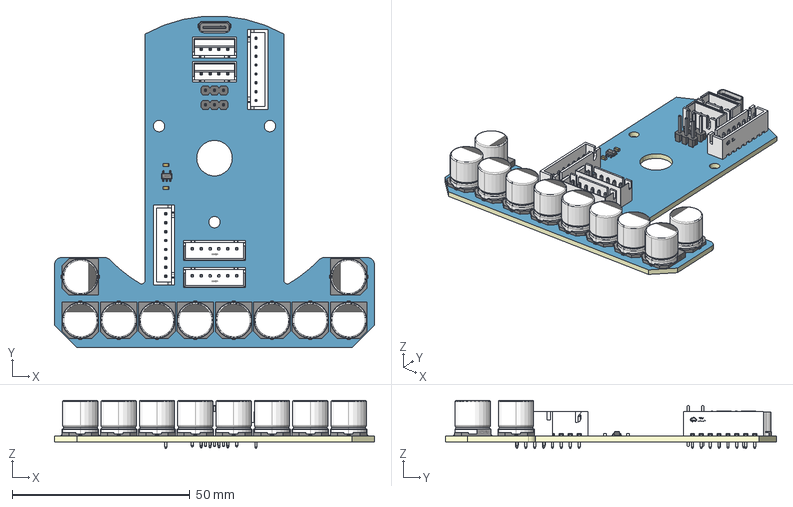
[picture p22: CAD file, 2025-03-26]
PCB/3D/3D_云台顶部分线板PCB_2025-03-11.step
90.0 x 93.2 x 13.5 mm
TopTrack
BottomTrack
Board

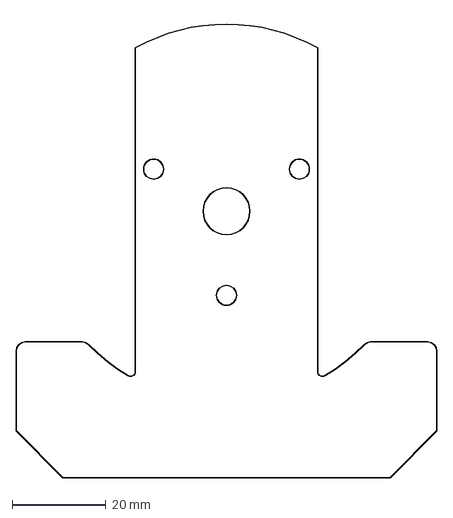
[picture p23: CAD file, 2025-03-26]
PCB/外形/云台top.DXF
90.0 x 98.7 mm

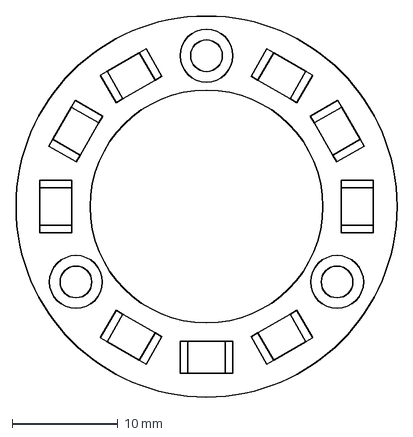
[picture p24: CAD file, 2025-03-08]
PCB/外形/灯光板.DXF
36.0 x 36.0 mm

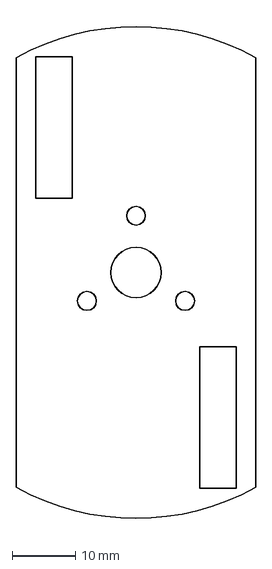
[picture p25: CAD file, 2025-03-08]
PCB/外形/机械臂分线板.DXF
38.0 x 81.3 mm

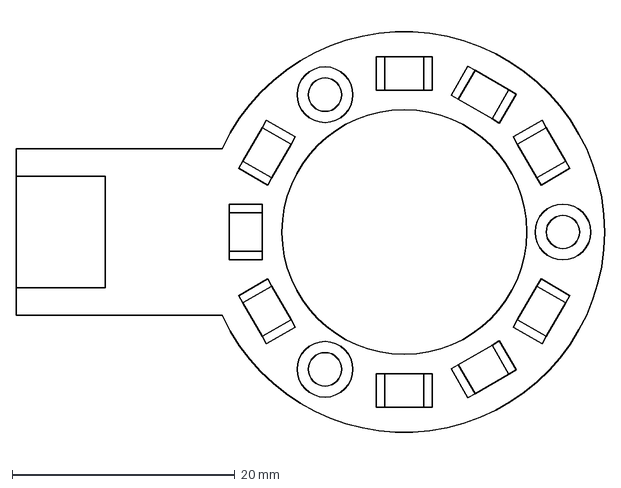
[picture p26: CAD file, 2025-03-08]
PCB/外形/灯光板2.0.DXF
52.9 x 38.8 mm

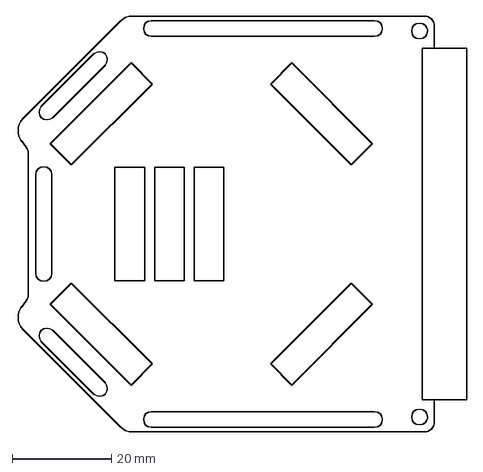
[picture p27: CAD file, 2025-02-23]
PCB/外形/分线板2.0.DXF
90.9 x 83.9 mm

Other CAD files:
PCB/外形/分线板2.0（正面）(1).DWG

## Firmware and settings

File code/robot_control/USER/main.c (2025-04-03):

#include "main.h"

/**
*@note 该工程启用了FPU加速浮点运算
*@note 使用DSP库加速部分运算
*/

/**
*@brief  延时任务，调试时使用，节点延时一定时间
*@param 无
*@return 无
*/
void task_delay(void)
{
    stop_Omni_Wheel();
    robot_arm_control_botton_speed(0);
    delay_ms(2000);
}

/**
*@brief  阻塞任务，调试时使用，阻塞整个程序
*@param 无
*@return 无
*/
void task_while()
{
    stop_Omni_Wheel();
    while(1);
}

/**
*@brief  空任务，规划路径时占位
*@param 无
*@return 无
*/
void void_task(void){};

int main(void)
{
    NVIC_PriorityGroupConfig(NVIC_PriorityGroup_2);	//中断优先级分组
    delay_init(168);
    system_clock_init();
    protocols_init();

    chassis_control_init();
	robot_arm_control_init();
    scanner_init();

    delay_ms(2000);
    robot_arm_reset_yz();

#if test_rotator_task

    gimbal_motor_set_speed_acc(500, 200);
    qr_data_packge[0] = '1';
    qr_data_packge[1] = '3';
    qr_data_packge[2] = '2';

    rotator_task_plus();
    while(1);

#endif

#if test_processing_task

    gimbal_motor_set_speed_acc(500, 100);
    qr_data_packge[0] = '1';
    qr_data_packge[1] = '3';
    qr_data_packge[2] = '2';

    processing_task_plus();

    while(1);
#endif

#if robot_arm_demonstration

    get_motor_angle(motor[4]);
    get_motor_angle(motor[5]);
    get_motor_angle(motor[6]);

    delay_ms(1000);

    robot_arm_pow_control(motor[4],DISABLE);
    robot_arm_pow_control(motor[5],DISABLE);
    robot_arm_pow_control(motor[6],DISABLE);

    while(1)
    {
        robot_arm_get_position();
        delay_ms(500);
    }

#endif
/*

        ^
        |x
        |
        ---->y

*/
//---------------------------time------dis---speed-----acc--------------//
    //创建x轴速度队列
    static li5_t node_x_speed[]={{0.0f, 0.0f, 0.0f, 0.0f, NULL},        //出发到扫码区域
                                 {1500.0f, 450.0f, 0.5f, 0.0f, NULL},
                                 {3000.0f, 700.0f, 0.0f, 0.0f, NULL},
                                 {.task =  qr_code_task},                 //扫码区域到转盘区域
                                 {3000.0f, 900.0f, 0.0f, 0.0f, NULL},

                                 {.task =  rotator_task_plus},               //转盘区域到粗加工区域
                                 {1500.0f, -450.0f, 0.0f, 0.0f, NULL},
                                 {6000.0f, -350.0f, 0.0f, 0.0f, NULL},
                                 {.task =  processing_task_plus},       //粗加工区域到精加工区域
                                 {2500.0f, 850.0f, 0.1f, 0.0f, NULL},
                                 {4000.0f, 900.0f, 0.0f, 0.0f, NULL},

                                 {.task =  processing_task_plus},       //精加工区到转盘
                                 {2000.0f, -100.0f, -0.2f, 0.0f, NULL},
                                 {4000.0f, -550.0f, 0.0f, 0.0f, NULL},

                                 //二程
                                 {.task =  rotator_task_plus},               //转盘区域到粗加工区
                                 {1500.0f, -450.0f, 0.0f, 0.0f, NULL},
                                 {6000.0f, -300.0f, 0.0f, 0.0f, NULL},          //!!!!!!!!!易出界
                                 {.task =  processing_task_plus},       //粗加工区域到精加工区域
                                 {2500.0f, 850.0f, 0.1f, 0.0f, NULL},
                                 {4000.0f, 900.0f, 0.0f, 0.0f, NULL},

                                 //回家
                                 {.task =  processing_task_plus},
                                 {6000.0f, -2000.0f, 0.0f, 0.0f, NULL},
                                 {9000.0f, -2100.0f, 0.0f, 0.0f, NULL},
                                 {.task =  &end_quene}};

    // //创建y轴速度队列
    static li5_t node_y_speed[]={{0.0f, 0.0f, 0.0f, 0.0f, NULL},        //出发到扫码区域
                                 {1500.0f, -200.0f, -0.1f, 0.0f, NULL},
                                 {3000.0f, -200.0f, 0.0f, 0.0f, NULL},
                                 {.task =  void_task},                  //扫码区域到转盘区域
                                 {3000.0f, 0.0f, 0.0f, 0.0f, NULL},

                                 {.task =  void_task},                  //转盘区域到粗加工区域
                                 {1500.0f, -200.0f, 0.0f, 0.0f, NULL},
                                 {6000.0f, -1900.0f, 0.0f, 0.0f, NULL},
                                 {.task =  void_task},                  //粗加工区域到精加工区域
                                 {2000.0f, 100.0f, 0.2f, 0.0f, NULL},
                                 {4000.0f, 950.0f, 0.0f, 0.0f, NULL},

                                 {.task =  void_task},                  //精加工区到转盘
                                 {2500.0f, 950.0f, 0.1f, 0.0f, NULL},
                                 {4000.0f, 1050.0f, 0.0f, 0.0f, NULL},

                                 //二程
                                 {.task =  void_task},                  //转盘区域到粗加工区
                                 {1500.0f, -200.0f, 0.0f, 0.0f, NULL},
                                 {6000.0f, -1900.0f, 0.0f, 0.0f, NULL},
                                 {.task =  void_task},                  //粗加工区域到精加工区域
                                 {2000.0f, 100.0f, 0.2f, 0.0f, NULL},
                                 {4000.0f, 950.0f, 0.0f, 0.0f, NULL},

                                 //回家
                                 {.task =  void_task},                  
                                 {6000.0f, -100.0f, 0.0f, 0.0f, NULL},        
                                 {9000.0f, 1000.0f, 0.0f, 0.0f, NULL},
                                 {.task =  &end_quene}};

    // //创建w轴速度队列
    static li5_t node_w_dis[] ={{0.0f, 0.0f, 0.0f, 0.0f, NULL},         //出发到扫码区域
                                {2500.0f, 0.0f, 0.0f, 0.0f, NULL},
                                {3000.0f, 0.0f, 0.0f, 0.0f, NULL},
                                {.dis= 0.0f, .task =  void_task},       //扫码区域到转盘区域
                                {3000.0f, -90.0f, 0.0f, 0.0f, NULL},
                                {.dis= -90.0f, .task =  void_task},     //转盘区域到粗加工区域
                                {1500.0f, -90.0f, 0.0f, 0.0f, NULL},
                                {6000.0f, 90.0f, 0.0f, 0.0f, NULL},
                                {.dis= 90.0f,.task =  void_task},       //粗加工区域到精加工区域
                                {2000.0f, 45.0f, 0.0f, 0.0f, NULL},
                                {4000.0f, 0.0f, 0.0f, 0.0f, NULL},
                                {.dis= 0.0f, .task =  void_task},       //精加工区到转盘
                                {2000.0f, -45.0f, 0.0f, 0.0f, NULL},
                                {4000.0f, -90.0f, 0.0f, 0.0f, NULL},
                                //二程
                                {.dis= -90.0f, .task =  void_task},     //转盘区域到粗加工区
                                {1500.0f, -90.0f, 0.0f, 0.0f, NULL},
                                {6000.0f, 90.0f, 0.0f, 0.0f, NULL},
                                {.dis= 90.0f,.task =  void_task},       //粗加工区域到精加工区域
                                {2000.0f, 45.0f, 0.0f, 0.0f, NULL},
                                {4000.0f, 0.0f, 0.0f, 0.0f, NULL},
                                //回家
                                {.task =  void_task},                    
                                {6000.0f, -90.0f, 0.0f, 0.0f, NULL},
                                {9000.0f, -90.0f, 0.0f, 0.0f, NULL},
                                {.dis= -90.0f,.task =  task_while},       
                                {.task =  &end_quene}};

//-------------------------------------end------------------------------//

    static path_quene_t x_speed = {.quene = node_x_speed,
                                   .timer.count_end_time = 0xFFFFFFFF};

    static path_quene_t y_speed = {.quene = node_y_speed,
                                   .timer.count_end_time = 0xFFFFFFFF};

    static path_quene_t w_dis = {.quene = node_w_dis,
                                 .timer.count_end_time = 0xFFFFFFFF};

    solve_li5th_node(x_speed.quene);
    solve_li5th_node(y_speed.quene);
    solve_li5th_node(w_dis.quene);

    start_count_time(&x_speed.timer);
    start_count_time(&y_speed.timer);
    start_count_time(&w_dis.timer);

    static float _x_speed = 0.0f, _y_speed = 0.0f, _w_dis = 0.0f;

    while(1)
    {
        if(timer_10ms_flag)
        {
            timer_10ms_flag = 0;

            _x_speed = chassis_path_control(&x_speed, out_type_speed);
            _y_speed = chassis_path_control(&y_speed, out_type_speed);
            _w_dis = chassis_path_control(&w_dis, out_type_displacement);

            chassis_control_Omni_Wheel(_x_speed, _y_speed, _w_dis);
            robot_arm_control_botton_speed_CL(_abs_robot_arm_angle);
        }
    }
}

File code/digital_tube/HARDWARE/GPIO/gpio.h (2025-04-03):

#ifndef __GPIO_H
#define __GPIO_H

#include "sys.h"
#include "delay.h"

//数码管GPIO定义
#define _8_LED_GPIO     GPIOA
#define A      			GPIO_Pin_0
#define B               GPIO_Pin_1
#define C               GPIO_Pin_2
#define D               GPIO_Pin_3
#define E               GPIO_Pin_4
#define F               GPIO_Pin_5
#define G               GPIO_Pin_6
#define DP              GPIO_Pin_7

#define _3_LED_GPIO     GPIOB       
#define A_DIG1          GPIO_Pin_0 
#define A_DIG2          GPIO_Pin_1 
#define A_DIG3          GPIO_Pin_2 
#define B_DIG1          GPIO_Pin_3 
#define B_DIG2          GPIO_Pin_4 
#define B_DIG3          GPIO_Pin_5 

#define all_reset       0xFF
#define all_set         0x00
#define show_1          0xF9
#define show_2          0xA4
#define show_3          0xB0
#define show_ERR        0x86

void _3_8_PIN_LED_Init(void);
void num_show(char data);
void LED_display(char *display_data, int delay_time);

#endif

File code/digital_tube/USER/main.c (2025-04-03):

#include "delay.h"
#include "sys.h"
#include "gpio.h"
#include "power.h"
#include "usart.h"

//display_data定义在usart.c文件

int main(void)
{
	delay_init();	    	 //延时函数初始化	  
	uart1_Init(115200);
	_3_8_PIN_LED_Init();
	
  while(1) 
	{
			for(int a = 100; a < 1000; a++)
				LED_display(display_data, a);
			for(int a = 1000; a > 100; a--)
				LED_display(display_data, a);
	}
}

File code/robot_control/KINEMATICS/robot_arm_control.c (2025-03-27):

#include "robot_arm_control.h"

/*
    机械臂控制
*/

static u8 robot_arm_motor_rx_data[30];          //电机返回数据缓存

static float degree_switch = 0.0f;              //实际角度转换电机脉冲系数
static float rad_2_angle = 0.0f;                //弧度转角度系数
static float angle_2_rad = 0.0f;                //角度转弧度系数
static float square_first_arm_lenght= 0.0f;    //大臂长度平方
static float square_second_arm_lenght= 0.0f;   //小臂长度平方

float gimbal_motor_1_position = 0;        //云台电机位置
float gimbal_motor_2_position = 0;        //云台电机位置
float gimbal_motor_3_position = 0;        //云台电机位置

/**
*@brief 机械臂控制初始化
*@param 无
*@return 无
*/
void robot_arm_control_init(void)
{
    servo_init();
    gimbal_motor_init();
    usart3_rx_dma_init(robot_arm_motor_rx_data, 20);

    robot_arm_pow_control(motor[4],ENABLE);
    robot_arm_pow_control(motor[5],ENABLE);
    robot_arm_pow_control(motor[6],ENABLE);

    motor_turn_to_zero(motor[4]);
    motor_turn_to_zero(motor[5]);
    motor_turn_to_zero(motor[6]);

    //常数参数计算
    rad_2_angle = 180.0f / PI;
    angle_2_rad = PI / 180.0f;
    degree_switch = 3200.0f / 360.0f * reduction_ratio;
    square_first_arm_lenght = first_arm_lenght * first_arm_lenght;
    square_second_arm_lenght = second_arm_lenght * second_arm_lenght;
}

/**
*@brief 机械臂底座角度控制
*@param degree: 云台绝对角度
*@return 无
*/
void robot_arm_control_botton_position(float degree)
{
    motor[5].acc_speed = 150;
    
    if(degree < 0)
    {
        motor[5].direction = 1;
        degree = -degree;
    }
    else
    {
        motor[5].direction = 0;
    }

    motor[5].pulse_num = (int)(degree * degree_switch + 0.5f);
    motor[5].speed = 300;

    gimbal_motor_control_position(motor[5]);
}

/**
*@brief 机械臂底座控制速度
*@param speed: 速度
*@return 无
*/
void robot_arm_control_botton_speed(float speed)
{
    if(speed < 0)
    {
        motor[5].direction = 0;
        speed = -speed;
    }
    else
    {
        motor[5].direction = 1;
    }

    motor[5].speed = (int)(speed + 0.5f);
    motor[5].acc_speed = 0;
    gimbal_motor_control_speed(motor[5]);
}

/**
*@brief 机械臂底座电机闭环控制速度
*@param targe: 机械臂保持的目标角度
*@return 无
*/
void robot_arm_control_botton_speed_CL(float targe)
{
    float abs_robot_arm_angle, err;

    get_motor_angle(motor[5]);

    abs_robot_arm_angle = gimbal_motor_2_position + abs_degree_data;

    // printf("%f %f %f\r\n", switch_angle, abs_degree_data, gimbal_motor_2_position);

    err = targe - abs_robot_arm_angle;

    printf("%f\r\n", err);

    err = err * -3.0f;

    if(err > 100) err = 100;
    else if(err < -100) err = -100;

    robot_arm_control_botton_speed(err);
}

/**
*@brief 机械大小臂角度控制
*@param first_arm_degree: 大臂相对角度
*@param second_arm_degree: 小臂相对角度
*@return 无
*/
void robot_arm_control_arm_poosition(float first_arm_degree, float second_arm_degree)
{
    if(first_arm_degree < 0)
    {
        motor[6].direction = 1;
        first_arm_degree = -first_arm_degree;
    }
    else
    {
        motor[6].direction = 0;
    }

    if(second_arm_degree < 0)
    {
        motor[4].direction = 1;
        second_arm_degree = -second_arm_degree;
    }
    else
    {
        motor[4].direction = 0;
    }

    motor[6].pulse_num = (int)(first_arm_degree * degree_switch + 0.5f);
    // motor[6].speed = 150;

    motor[4].pulse_num = (int)(second_arm_degree * degree_switch + 0.5f);
    // motor[4].speed = 150;

    gimbal_motor_control_position(motor[4]);
    gimbal_motor_control_position(motor[6]);
}

/**
*@brief yz平面机械臂运动学逆解算
*@param y: y轴运动距离
*@param z: z轴运动距离
*@param out_arm_degree[0]: 大臂角度,竖直方向为0,向前为正角度
*@param out_arm_degree[1]: 小臂角度,水平方向为0,向上为正角度
*@return void
*/
void robot_arm_calculate_inverse(float y, float z, float* out_arm_degree)
{
    float   first_arm_degree,       //大臂角度
            second_arm_degree,      //小臂角度
            first_arm_rad_1,        //大臂弧度计算中间值1
            first_arm_rad_2,        //大臂弧度计算中间值2
            short_side,             //短边
            hypotenuse;             //斜边   

    //考虑爪子长度高度,修正坐标系
    y = y - gripper_lenght; 
    z = z + gripper_height;
    if(y < 0) y = 0;

    //计算斜边
    short_side = base_height - z;
    if(short_side < 0) short_side = short_side * -1.0f;
    arm_sqrt_f32(short_side * short_side + y * y, &hypotenuse);

    //计算大臂中间值1弧度
    first_arm_rad_1 = acos((square_first_arm_lenght  -
                            square_second_arm_lenght + 
                            hypotenuse * hypotenuse) /
                            (2.0f * first_arm_lenght * hypotenuse));

    //计算大臂中间值2弧度
    //bug:有 -PI/2.0f 输出数据才正常
    if(base_height > z) first_arm_rad_2 = atan(y / short_side) - PI / 2.0f;
    else if(base_height < z) first_arm_rad_2 = atan(short_side / y);
    else first_arm_rad_2 = 0.0f;

    //大臂角度计算
    first_arm_degree = (first_arm_rad_1 + first_arm_rad_2) * rad_2_angle;

    //小臂角度计算
    second_arm_degree = acos((square_first_arm_lenght  +
                              square_second_arm_lenght -
                              hypotenuse * hypotenuse) /
                              (2.0f * first_arm_lenght * second_arm_lenght)) * 
                              rad_2_angle;

    first_arm_degree = 90.0f - first_arm_degree;
    second_arm_degree = -90.0f + second_arm_degree - first_arm_degree;

    out_arm_degree[0] = first_arm_degree;   //大臂角度
    out_arm_degree[1] = second_arm_degree;  //小臂角度
}

/**
*@brief 机械臂运动学正解算
*@param first_arm_degree: 大臂角度,竖直方向为0,向前为正角度
*@param second_arm_degree: 小臂角度,水平方向为0,向上为正角度
*@param out_arm_location_yz[0]: 输出坐标y
*@param out_arm_location_yz[1]: 输出坐标z
*@return void
*/
float* robot_arm_calculate_forward(float first_arm_degree, float second_arm_degree, float* out_arm_location_yz)
{
    float z1, z2, y1, y2;                                   //大臂和小臂的z轴和y轴增量

    z1 = first_arm_lenght * arm_cos_f32(first_arm_degree * angle_2_rad);
    y1 = first_arm_lenght * arm_sin_f32(first_arm_degree * angle_2_rad);
                                                                                    
    z2 = second_arm_lenght * arm_sin_f32(second_arm_degree * angle_2_rad);
    y2 = second_arm_lenght * arm_cos_f32(second_arm_degree * angle_2_rad);

    out_arm_location_yz[0] = y1 + y2 + gripper_lenght;
    out_arm_location_yz[1] = z1 + z2 - gripper_height + base_height;

    return out_arm_location_yz;
}

/**
*@brief 机械臂yz平面位置控制
*@param y: y坐标,单位mm
*@param z: z轴坐标,单位mm
*@return void
*/
void robot_arm_control_yz(float y, float z)
{
    float yz_to_angle[2];
    
    robot_arm_calculate_inverse(y, z, yz_to_angle);
    robot_arm_control_arm_poosition(yz_to_angle[0], yz_to_angle[1]);
}

/**
*@brief 获取电机当前位置
*@return void
*/
void robot_arm_get_position(void)
{
    get_motor_angle(motor[4]);
    get_motor_angle(motor[5]);
    get_motor_angle(motor[6]);

    delay_ms(10);
}

/**
*@brief 等待所有电机运动完毕
*@return void
*/
void robot_arm_wait_stop(void)
{
    get_motor_state(motor[6]);
    delay_ms(10);
}
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

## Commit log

2025-02-23 初次提交
    [分线板2.0.DXF, 分线板2.0（正面）(1).DWG]
2025-03-08 修改readme
2025-03-08 移除pdf
2025-03-08 正在调试机械臂示教功能
2025-03-08 增加整体视图
2025-03-08 todo修改
2025-03-08 增加整体视图2
2025-04-03 最终程序提交
2025-04-03 最终提交
2025-04-03 删除不必要文件
